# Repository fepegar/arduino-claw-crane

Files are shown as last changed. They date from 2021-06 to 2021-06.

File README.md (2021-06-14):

# The Claw Crane

Collaboration with artist
[Estefanía B. Flores](https://www.instagram.com/estefantastic)
for her master's thesis at
[Goldsmiths, University of London](https://www.gold.ac.uk/).

Old arcade claw crane controlled with an
[Arduino UNO](https://store.arduino.cc/arduino-uno-rev3) microcontroller board.

<p align="center">
  
</p>

[Video on YouTube](https://youtu.be/3AYCTyHq7pU)

[Photos](./photos)

[Videos](./videos)

## Diagrams

### Breadboard

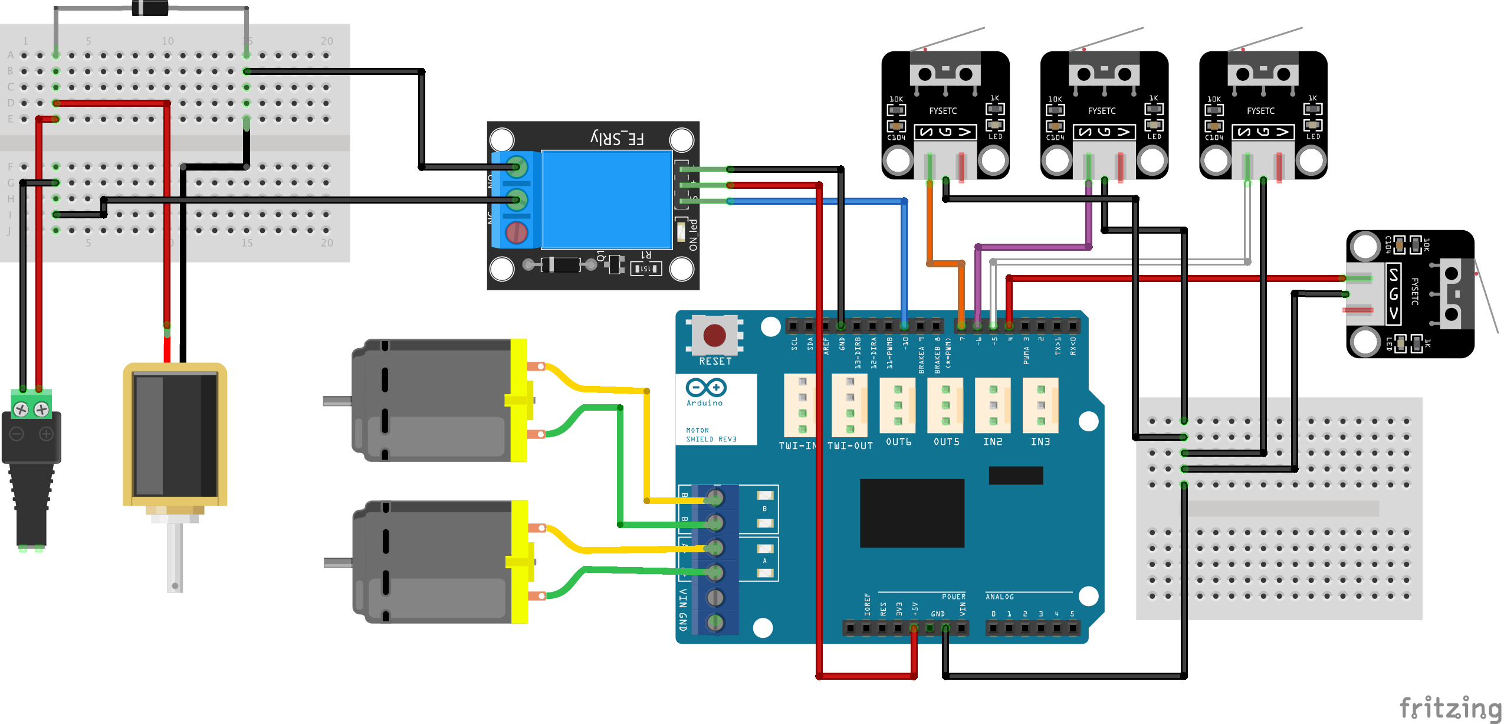
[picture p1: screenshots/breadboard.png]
Breadboard


### Schematic

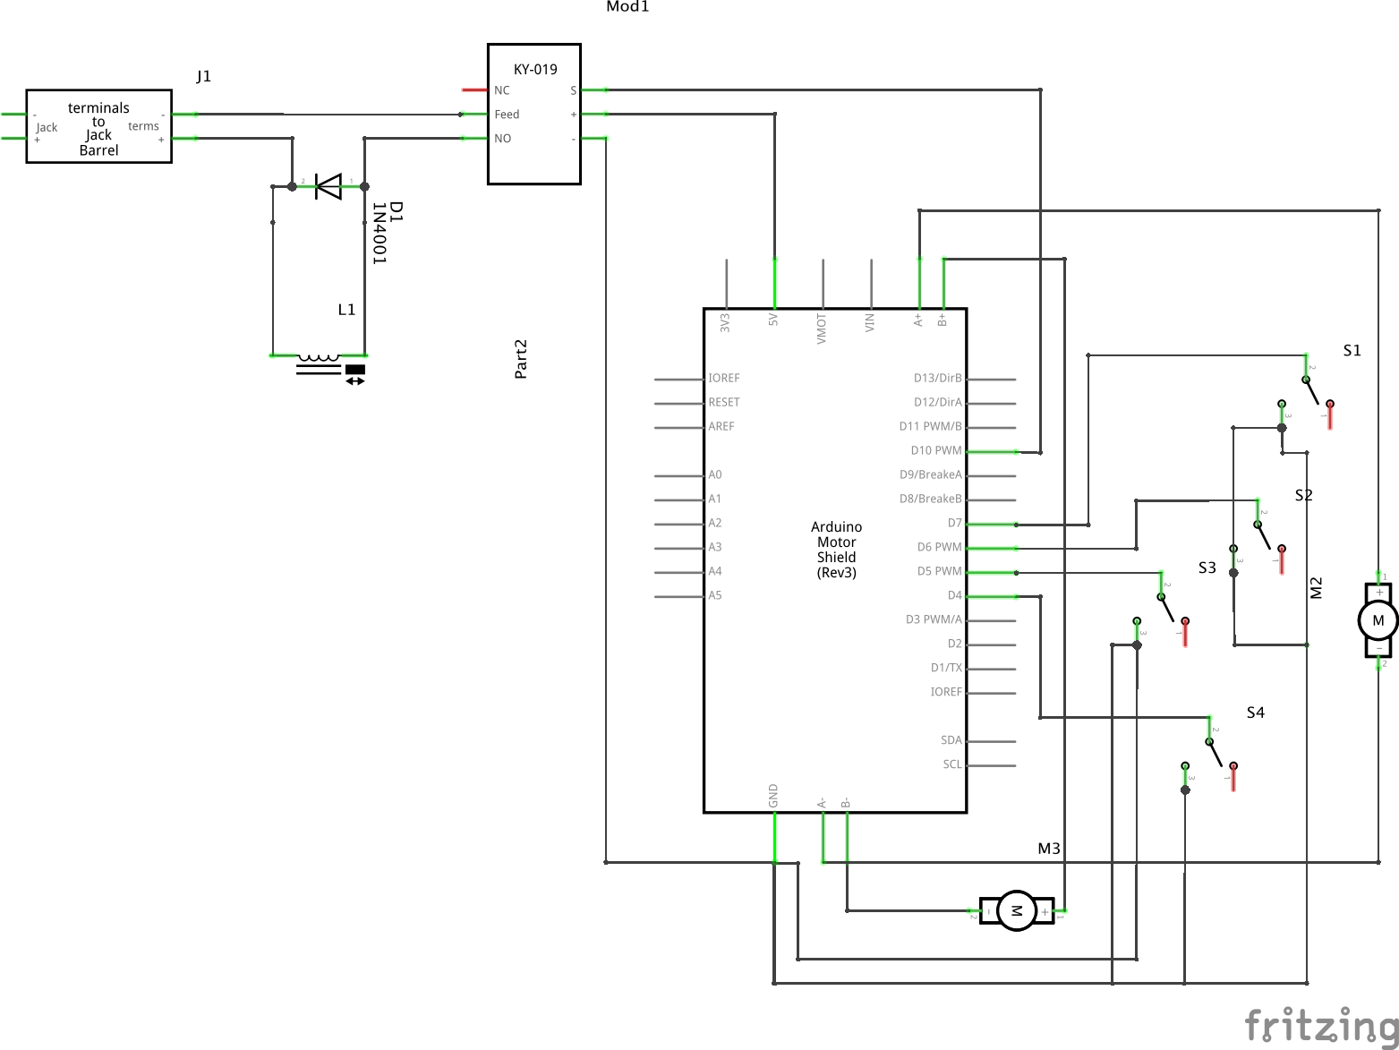
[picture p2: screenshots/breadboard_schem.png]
Schematic


## Motors

There are three DC motors, but we will only use two.

<p align="center">
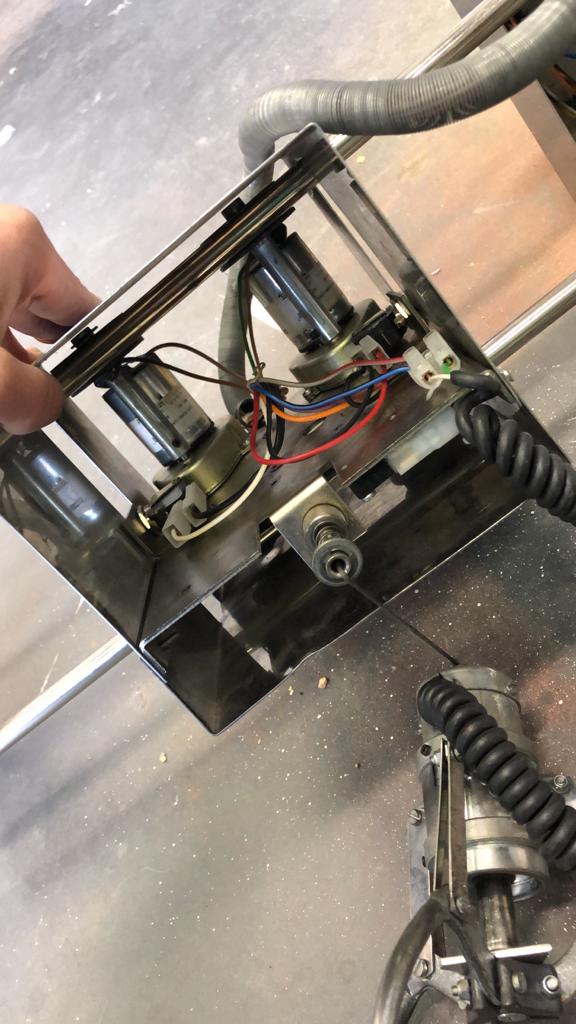
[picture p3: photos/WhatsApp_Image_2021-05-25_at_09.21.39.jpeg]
  
</p>

They seem to be [12V Crouzet DC brush geared motors (828610)](https://soda.crouzet.com/pn/?i=82861009).

<p align="center">
  
</p>

I used an [Arduino motor shield](https://store.arduino.cc/arduino-motor-shield-rev3)
to control them.

<p align="center">
  
</p>

Each motor has two associated limit switches. They are connected to the Arduino
using internal pull-up resistors.

<p align="center">
  
</p>

<p align="center">
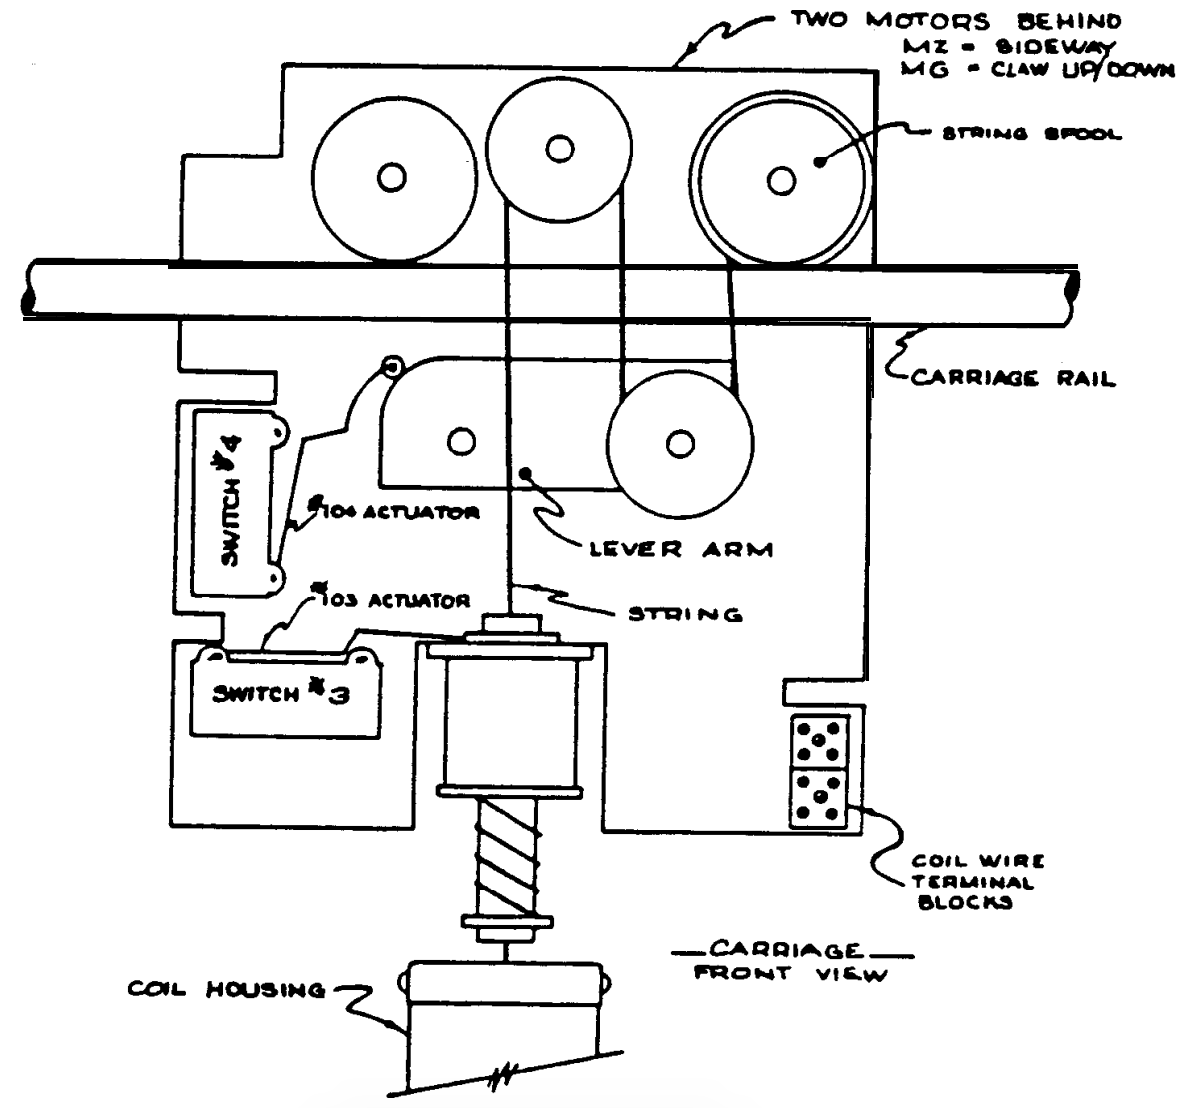
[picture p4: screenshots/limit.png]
  
</p>

(From [this manual](http://ohwow-arcade.com/Assets/Game_Manuals/BIG%20CHOICE.PDF))

## Claw solenoid

The claw is closed using a push solenoid.

To control the claw, I used a relay module. More specifically, I used a
[SunFounder 2-Channel DC 5V Relay Module with Optocoupler Low Level Trigger Expansion Board](https://www.sunfounder.com/products/2channel-relay-module).

<p align="center">
  
</p>

An ohmeter says the resistance across the solenoid is 4.5 ohms, so the current
through it will be 2.67 amps, as we are using 12 V.
We close the claw for 50 ms.

A flyback diode (1N4007) is placed in parallel to the claw to protect the
circuit.
According to [components101.com](https://components101.com/diodes/1n4007-diode),
the non-repetitive peak current is 30 amps, so it should be fine.

I decided to leave the jumper between Vcc and JD-Vcc in place (i.e., the current
for the relay solenoid is supplied through the Arduino pin). Ideally, though,
this voltage would come from an external power supply (good explanation
[in this video](https://youtu.be/d9evR-K6FAY)).

## Manual control

For testing, I used the joystick that comes with the Elegoo starter kit.
It seems to be a [KY-023](https://www.cricklewoodelectronics.com/Dual-axis-joystick-module-for-Arduino-KY-023.html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).

<p align="center">
  
</p>

More info:

- [Components101.com](https://components101.com/modules/joystick-module)
- [Arduinomodules.info](https://arduinomodules.info/ky-023-joystick-dual-axis-module/)

I use the potentiometers to control the two motors, and the push button to close
the claw.

## Links of interest

### Claw cranes

- [Holland Computers, Inc. – Crane Kit Manual – Part Number RA-CRANE-KIT](https://www.hollandcomputers.com/data/Gaming/Crane%20Kit%20Manual%20RA-CRANE-KIT-2019.pdf)
- [BBTSON MICROPROCESSOR CRANE](http://ohwow-arcade.com/Assets/Game_Manuals/BIG%20CHOICE.PDF)
- [Coast to Coast Entertainment – Stage 1 Crane Controller – D9803D4 Instructions](https://coasttocoastcranes.com/Manuals/Double%20Feature%20Manual.pdf)
- [Grayhound Electronics – The Crane Operators Manual](https://www.arcade-museum.com/manuals-vending/Grayhound_Crane_Schematics.pdf)
- [Grayhound crane dip switch settings](https://www.arcade-museum.com/manuals-vending/GrayhoundSkillCrane.pdf)
- [ArcadeControls.com – "greyhound crane claw problem"](http://forum.arcadecontrols.com/index.php?topic=111859.0)
- [Hackaday.io – Toy Claw Machine](https://hackaday.io/project/215-toy-claw-machine)
- [Fixing an 80's Drew's Tiger Paw Plush Crane Claw Machine With Schematics](https://www.youtube.com/watch?v=LLF4t5Sr2Ww)
- [Arcade Claw Machine/ Prize Game with Arduino](http://www.retrobuiltgames.com/the-build-page/arduino-claw-machine/)
- [Powering a crane/claw](https://electronics.stackexchange.com/questions/471259/powering-a-crane-claw)
- [Claw machines are rigged — here's why it's so hard to grab that stuffed animal](https://www.vox.com/2015/4/3/8339999/claw-machines-rigged)
- [Arduino Claw Machine](https://www.instructables.com/Arduino-Claw-Machine/)

### Arduino

- [DroneBot Workshop](https://www.youtube.com/channel/UCzml9bXoEM0itbcE96CB03w)
- [Paul McWhorter](https://www.youtube.com/channel/UCfYfK0tzHZTpNFrc_NDKfTA)
- [Robojax](https://www.youtube.com/channel/UCkcBSig_Iu4ZnAIeCeG1TVg)
- [Library tutorial](https://www.arduino.cc/en/Hacking/libraryTutorial)
- [Adafruit-BMP085-Library](https://github.com/adafruit/Adafruit-BMP085-Library)
- [API style guide](https://www.arduino.cc/en/Reference/APIStyleGuide)

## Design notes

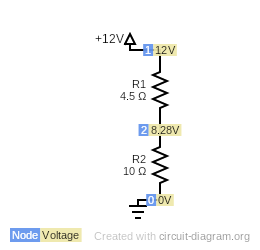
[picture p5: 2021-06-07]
screenshots/claw-simulation.png

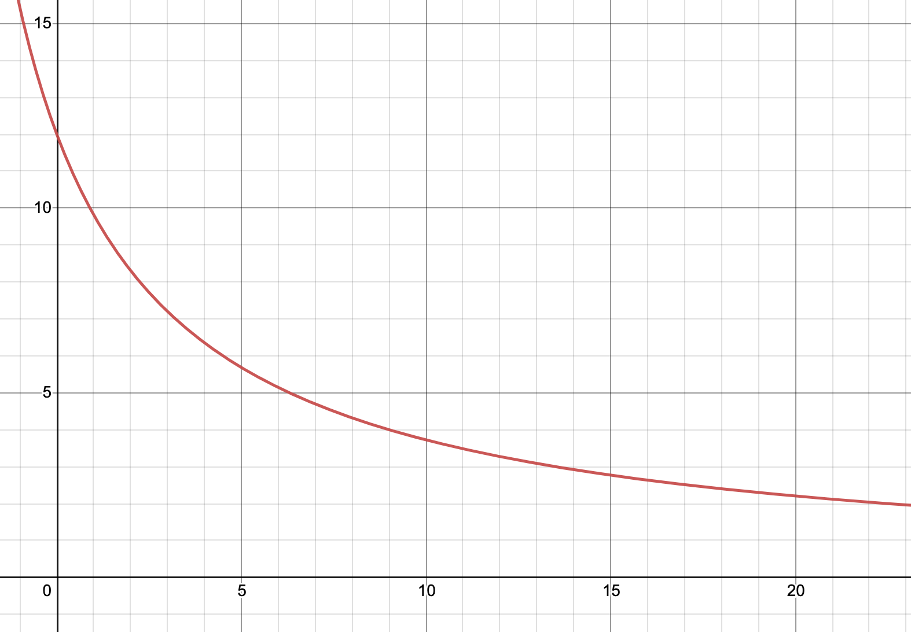
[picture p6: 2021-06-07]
screenshots/r2.png

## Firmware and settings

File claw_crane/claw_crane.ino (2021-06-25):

/*

  Joystick:
  - VRx to A3
  - VRy to A4
  - SW to A5

  Crane:
  - Motor x: orange-white, green
    - Pin 4 to pull-up resistor 10k to red (xLimit0)
    - Pin 5 to pull-up resistor 10k to white (xLimit1)
  - Motor y: orange-black, pink
    - Pin 6 to pull-up resistor 10k to purple (yLimitDown)
    - Pin 7 to pull-up resistor 10k to orange (yLimitUp)
  - Claw:
    - Pin 10 to relay module input 1
    - Claw solenoid to relay output
    - Arduino 5V used to power relay (risky?)

  - Speed X:
   - Positive speed is away from the motors
   - Negative speed is towards the motors

*/

#include "motor.h"
#include "joystick.h"
#include "claw.h"

#define MANUAL 0
#define AUTO 1

const int xLimitPin0 = 4;
const int xLimitPin1 = 5;

const int yLimitPinDown = 6;
const int yLimitPinUp = 7;

const int joystickPinX = A3;
const int joystickPinY = A4;
const int joystickPinPush = A5;

const int clawPin = 10;

Motor motorX(
  'X',
  ConstantsMotorB::directionPin,
  ConstantsMotorB::pwmPin,
  ConstantsMotorB::brakePin,
  ConstantsMotorB::currentPin,
  xLimitPin0,
  xLimitPin1
);

Motor motorY(
  'Y',
  ConstantsMotorA::directionPin,
  ConstantsMotorA::pwmPin,
  ConstantsMotorA::brakePin,
  ConstantsMotorA::currentPin,
  yLimitPinDown,
  yLimitPinUp
);

Joystick joystick(joystickPinX, joystickPinY, joystickPinPush);

Claw claw(clawPin);

float speedX;
float speedY;
boolean buttonPressed = false;

const int mode = AUTO;

void setup() {
  Serial.begin(9600);
}

void loop() {
  if (mode == AUTO) {
    motorX.moveAutoX();
    motorY.moveAutoY();
    claw.moveAuto();
  } else if (mode == MANUAL) {
    readJoystick();
    update();
  }
}


void readJoystick() {
  speedX = joystick.readX();
  speedY = joystick.readY();
  buttonPressed = joystick.readButton();
}


void update() {
  motorX.setSpeed(speedX);
  motorY.setSpeed(speedY);
  claw.setEnabled(buttonPressed);
}

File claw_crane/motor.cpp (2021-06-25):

#include "Arduino.h"
#include "motor.h"
#include "limit.h"


Motor::Motor(char motorID, int directionPin, int pwmPin, int brakePin, int currentPin, int limitPin0, int limitPin1)
{
  _motorID = motorID;

  pinMode(directionPin, OUTPUT);
  _directionPin = directionPin;

  pinMode(pwmPin, OUTPUT);
  _pwmPin = pwmPin;

  pinMode(brakePin, OUTPUT);
  _brakePin = brakePin;

  pinMode(currentPin, INPUT);
  _currentPin = currentPin;

  _ptrLimitSwitch0 = new LimitSwitch('0', limitPin0);
  _ptrLimitSwitch1 = new LimitSwitch('1', limitPin1);
  _ptrLimitSwitch0->begin();
  _ptrLimitSwitch1->begin();

  _moving = false;
  _timeToMove = millis() + _getRandomStopInterval();
  Serial.print("Time to move: ");
  Serial.println(_timeToMove);

  _speed = 0;
  _direction = 1;  // for motor Y (we don't really know if this is up or down)
  _timeLastLimit = -30000;
}

void Motor::stop() {
  _enableBrake();
  _setSpeed(0);
}

void Motor::moveAutoX() {
  boolean isMoving = _speed != 0;
  if (isMoving) {
    boolean mustStop = millis() >= _timeToStop;
    boolean limitReached = _getLimitSwitchFromSpeed(_speed)->isPushed();
    if (mustStop || limitReached) {
      Serial.println("Time to stop: " + String(mustStop));
      Serial.println("Limit reached: " + String(limitReached));
      Serial.println("Current speed: " + String(_speed));
      stop();
      unsigned long waitingTime = _getRandomStopInterval();
      _timeToMove = millis() + waitingTime;
      Serial.println("Stopping " + String(_motorID) + " for " + String(waitingTime));
      Serial.println();
    }
  } else if ((_speed == 0) && (millis() >= _timeToMove)) {
    float speed = _getRandomSpeed();
    Serial.println("Setting new speed: " + String(speed));
    _setSpeed(speed);
    unsigned long movingTime = _getRandomMoveInterval();
    _timeToStop = millis() + movingTime;
    Serial.println("Moving " + String(_motorID) + " at speed " + String(speed) + " for " + String(movingTime));
    Serial.println();
  }
}

void Motor::moveAutoY() {
  // When the claw goes all the way down, the thread starts winding in the opposite direction.
  // Therefore, the meaning of the velocities is swapped. We will just always go the same way
  // and change direction once the switch is activated. We will assume that only the limit
  // switch at the top will ever be enabled.
  boolean isMoving = _speed != 0;
  if (isMoving) {
    boolean mustStop = millis() >= _timeToStop;
    boolean limitReached = _ptrLimitSwitch1->isPushed();
    if (mustStop || limitReached) {
      Serial.println("Time to stop!");
      Serial.println("Time reached: " + String(mustStop));
      Serial.println("Limit reached: " + String(limitReached));
      if (limitReached) {
        unsigned long timeSinceLast = millis() - _timeLastLimit;
        if (timeSinceLast > 30000) {  // So it doesn't get stuck at the top
          Serial.println("Top limit switch reached. Changing direction...");
          _direction *= -1;
          Serial.println("_direction is " + String(_direction));
          _timeLastLimit = millis();
        }
      }
      Serial.println("Current speed: " + String(_speed));
      stop();
      unsigned long waitingTime = _getRandomStopInterval();
      _timeToMove = millis() + waitingTime;
      Serial.println("Stopping " + String(_motorID) + " for " + String(waitingTime));
      Serial.println();
    }
  } else if ((!isMoving) && (millis() >= _timeToMove)) {
    Serial.println("Time to move!");
    float speed = _getRandomSpeed();
    speed = abs(speed);  // docs for abs() say it should be done like this
    speed *= _direction;
    Serial.println("Setting new speed: " + String(speed));
    _setSpeed(speed);
    unsigned long movingTime = _getRandomMoveInterval();
    _timeToStop = millis() + movingTime;
    Serial.println("Moving " + String(_motorID) + " at speed " + String(speed) + " for " + String(movingTime));
    Serial.println();
  }
}

float Motor::getMilliAmps() {
  float voltage = _getVoltageFromPin();
  return _getCurrentFromVoltage(voltage);
}

void Motor::setSpeed(float speed) {
  if (speed == 0) {
    _setSpeed(0);
    return;
  }
  LimitSwitch* limitSwitch = _getLimitSwitchFromSpeed(speed);
  if (limitSwitch->isPushed()) {
    Serial.println("Cannot set speed " + String(speed) + " as limit switch " + String(limitSwitch->switchID) + " is pushed");
    _setSpeed(0);
  } else {
    Serial.println("Setting speed: " + String(speed));
    _setSpeed(speed);
  }
}

void Motor::_setSpeed(float speed) {
  _speed = speed;
  // Speed should be in [-1, 1]
  if (speed == 0) {
    _enableBrake();
  } else {
    _disableBrake();
    if (speed < 0) {
      speed *= -1;
      _setDirection(-1);
    } else {
      _setDirection(1);
    }
  }
  analogWrite(_pwmPin, _speedToByte(speed));
}

LimitSwitch* Motor::_getLimitSwitchFromSpeed(float speed) {
  LimitSwitch* limitSwitch;
  if (speed < 0) {
    limitSwitch = _ptrLimitSwitch0;
  } else if (speed > 0) {
    limitSwitch = _ptrLimitSwitch1;
  } else {
    limitSwitch = nullptr;
  }
  return limitSwitch;
}

void Motor::_enableBrake() {
  digitalWrite(_brakePin, HIGH);
}

void Motor::_disableBrake() {
  digitalWrite(_brakePin, LOW);
}

void Motor::_setDirection(int direction) {
  if (direction == -1) {
    digitalWrite(_directionPin, LOW);
  } else if (direction == 1) {
    digitalWrite(_directionPin, HIGH);
  }
}

int Motor::_speedToByte(float speed)
{
  float rescaled = 255 * speed;
  return int(rescaled);
}

float Motor::_getVoltageFromPin() {
  int lecture = analogRead(_currentPin);
  float voltage = float(lecture) / MAX_10_BITS * MAX_INPUT_VOLTAGE;
  return voltage;
}

float Motor::_getCurrentFromVoltage(float voltage) {
  float current = voltage / VOLTAGE_AT_MAX_CURRENT * CURRENT_AT_MAX_VOLTAGE;
  return current;
}

float Motor::_getRandomSpeed() {
  float x, m, n, y;
  x = _getRandomFloat();
  m = MAX_RANDOM_SPEED - MIN_RANDOM_SPEED;
  n = MIN_RANDOM_SPEED;
  y = m * x + MIN_RANDOM_SPEED;
  if (random(2) == 0) {
    y *= -1;
  }
  if (y < 0 && _ptrLimitSwitch0->isPushed()) {
    Serial.println("Flipping speed as switch 0 is enabled");
    y *= -1;
  } else if (y > 0 && _ptrLimitSwitch1->isPushed()) {
    Serial.println("Flipping speed as switch 1 is enabled");
    y *= -1;
  }
  return y;
}

float Motor::_getRandomFloat() {
  return random(0, 100000) / 100000.0;
}

unsigned long Motor::_getRandomStopInterval() {
  return random(MIN_STOP_INTERVAL, MAX_STOP_INTERVAL);
}

unsigned long Motor::_getRandomMoveInterval() {
  return random(MIN_MOVE_INTERVAL, MAX_MOVE_INTERVAL);
}

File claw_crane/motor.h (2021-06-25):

#ifndef motor_h
#define motor_h

#include "Arduino.h"
#include "limit.h"

#define VERBOSE 1

// Docs say 3.3 V for 2 A
#define CURRENT_AT_MAX_VOLTAGE 2
#define VOLTAGE_AT_MAX_CURRENT 3.3

#define MAX_10_BITS 1023
#define MAX_INPUT_VOLTAGE 5

#define MIN_RANDOM_SPEED 0.75
#define MAX_RANDOM_SPEED 1

#define MIN_STOP_INTERVAL 2000  // 2 s
#define MAX_STOP_INTERVAL 10000  // 10 s

#define MIN_MOVE_INTERVAL 500  // 0.2 s
#define MAX_MOVE_INTERVAL 2000 // 2 s


class Motor {
  public:
    Motor(char motorID, int directionPin, int pwmPin, int brakePin, int currentPin, int limitPin0, int limitPin1);
    void setSpeed(float speed);
    void stop();
    float getMilliAmps();
    boolean limitSwitchIsPushed(int direction);
    void moveAutoX();
    void moveAutoY();
    boolean _limitReached();

  private:
    char _motorID;
    int _pwmPin;
    int _directionPin;
    int _brakePin;
    int _currentPin;
    int _delayTime;
    float _speed;
    void _setSpeed(float speed);
    void _setDirection(int direction);
    int _speedToByte(float speed);
    void _enableBrake();
    void _disableBrake();
    float _getVoltageFromPin();
    float _getCurrentFromVoltage(float voltage);
    int _getCurrentDirection();
    LimitSwitch* _getLimitSwitchFromSpeed(float speed);
    LimitSwitch* _getRelevantLimitSwitch();
    float _getRandomSpeed();
    float _getRandomFloat();
    unsigned long _getRandomStopInterval();
    unsigned long _getRandomMoveInterval();
    unsigned long _timeToMove;
    unsigned long _timeToStop;
    boolean _moving;
    LimitSwitch* _ptrLimitSwitch0;
    LimitSwitch* _ptrLimitSwitch1;
    int _direction;
    long _timeLastLimit;
};


namespace ConstantsMotorA
{
  const int directionPin = 12;
  const int pwmPin = 3;
  const int brakePin = 9;
  const int currentPin = A0;
}


namespace ConstantsMotorB
{
  const int directionPin = 13;
  const int pwmPin = 11;
  const int brakePin = 8;
  const int currentPin = A1;
}

#endif

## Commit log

2021-06-01 Add Fritzing files
    [breadboard.fzz]
2021-06-03 Fix pin names
2021-06-03 Create motor and joystick libraries
2021-06-05 Add solenoid control
2021-06-05 Add claw class
2021-06-05 Disable claw when stopping all
2021-06-07 Add solenoid equations
2021-06-07 Add simulation of claw circuit
2021-06-07 Add claw circuit
2021-06-07 Add Arduino links
2021-06-10 Motors moving randomly
2021-06-10 Claw moving automatically as well
2021-06-10 Use Arduino syntax for casting
2021-06-12 Add some claw connections
2021-06-13 Update schematics
    [breadboard.fzz]
2021-06-13 Update schematics on README
2021-06-13 Fix schematics paths
2021-06-13 Add info on flyback diode
2021-06-25 Fix auto mode for y axis
    [claw.cpp, claw_crane.ino, motor.cpp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]
